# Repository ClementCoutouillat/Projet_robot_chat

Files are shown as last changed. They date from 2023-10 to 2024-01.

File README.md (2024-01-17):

# Projet_robot_chat

Projet fait par Quentin Henriet, Bastien Chinianga, Jiang Kaixuan, Jangbo Wang et Clément Coutouillat
Dans ce projet, nous devons réaliser un robot à propulsion différentielle à deux roues pour jouer au jeu du chat et de la souris. Lorsque le robot est le chat, il poursuit la souris, et lorsqu'il est la souris, il fuit le chat. Pour accomplir ce jeu, nous devons réaliser les parties suivantes :

- Le robot doit pouvoir changer de rôle entre chat et souris dans le jeu. Lorsque deux robots entrent en collision, leurs rôles changent - capteur de détection de collision.
- Le robot doit pouvoir se déplacer dans un environnement avec des limites, donc nous avons besoin d'un capteur de détection de bord - capteur de détection de bord.
- Le robot doit pouvoir détecter le chat ou la souris sur le terrain, donc nous avons besoin d'un capteur pour détecter les objets sur le terrain - capteur LIDAR.

## Ydlidar

Nous utilisons le LIDAR YDLIDAR X4 pour détecter l'autre robot sur le terrain.
D'après le manuel de données de YDLIDAR, nous savons que YDLIDAR utilise Uart pour la communication. Dans le manuel de développement, nous pouvons obtenir le format des données du LIDAR, comme illustré ci-dessous :
Lorsque nous envoyons la commande A5 60 au LIDAR, il renvoie une trame de données, dont le format est illustré ci-dessous :
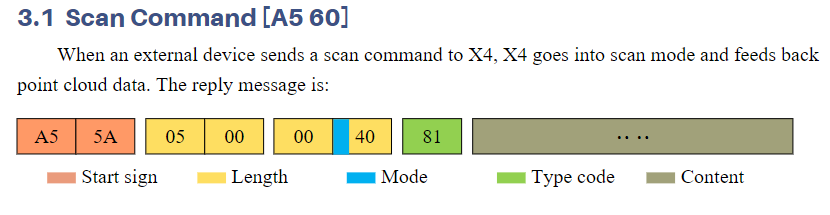
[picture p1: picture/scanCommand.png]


Ensuite, en suivant la méthode d'analyse du manuel de développement, nous obtenons les angles et les distances des obstacles de 0 à 360 degrés autour du robot, ce qui nous permet de localiser l'autre robot.
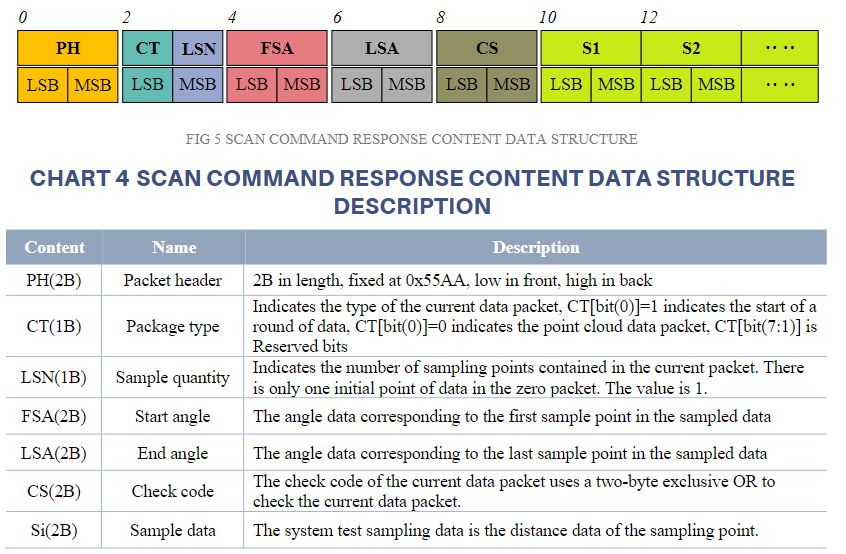
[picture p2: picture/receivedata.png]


## Stratégie

Dans le jeu, lorsque le robot est le chat, il doit poursuivre la souris, et lorsqu'il est la souris, il doit fuir le chat. Donc, selon le rôle du robot, nous avons besoin de stratégies différentes pour contrôler le mouvement du robot.

### Stratégie Chat

Lorsque le robot est le chat, il doit poursuivre la souris. Nous devons donc faire bouger le robot dans la direction de la souris. Tout d'abord, nous contrôlons la rotation du robot en calculant la différence d'angle entre le robot et la souris. Lorsque la souris se trouve entre 0 et 180 degrés, nous faisons tourner le robot à gauche. Lorsque l'autre robot se trouve entre 180 et 360 degrés, nous faisons tourner le robot

à droite. Une fois que le robot est orienté correctement, nous le faisons avancer jusqu'à ce qu'il entre en collision avec la souris. À ce moment-là, le rôle du robot change : le robot devient la souris et l'autre robot devient le chat. Nous pouvons alors utiliser la stratégie de la souris pour contrôler le mouvement du robot.

### Stratégie Souris

Lorsque le robot est la souris, il doit fuir le chat. Nous devons donc faire éloigner le robot du chat. Lorsqu'un chat se trouve à moins de 50 cm du robot et qu'il est situé entre 0 et 180 degrés, nous faisons tourner le robot à gauche de 90 degrés, puis le faisons avancer sur une certaine distance avant de le faire tourner à droite de 90 degrés. Cela permet au robot de s'éloigner du chat. Lorsque la distance entre le robot et le chat dépasse 50 cm, nous arrêtons le mouvement du robot. Lorsque le chat est situé entre 180 et 360 degrés, nous faisons tourner le robot à droite de 90 degrés, puis à gauche de 90 degrés, pour lui permettre de s'éloigner du chat.

## Moteur

Nous utilisons un robot à propulsion différentielle à deux roues, donc nous devons contrôler la vitesse des roues gauche et droite pour diriger le robot. Nous utilisons un moteur à courant continu à engrenages avec encodeur, dont la vitesse maximale est de 300 RPM.

### Avancer

Pour faire avancer le robot en ligne droite, nous contrôlons les vitesses des roues gauche et droite pour qu'elles soient identiques.

### Tourner

Le robot tourne en contrôlant la différence de vitesse entre les roues gauche et droite. Lorsque les vitesses des roues sont différentes, le robot tourne.

Nous utilisons une vitesse fixe pour contrôler la direction du robot. Lorsque le robot doit tourner à gauche, nous fixons la vitesse de la roue gauche à 0 et celle de la roue droite à la vitesse maximale. Lorsque le robot doit tourner à droite, nous fixons la vitesse de la roue droite à 0 et celle de la roue gauche à la vitesse maximale. Le temps nécessaire pour tourner est calculé avec la formule suivante :
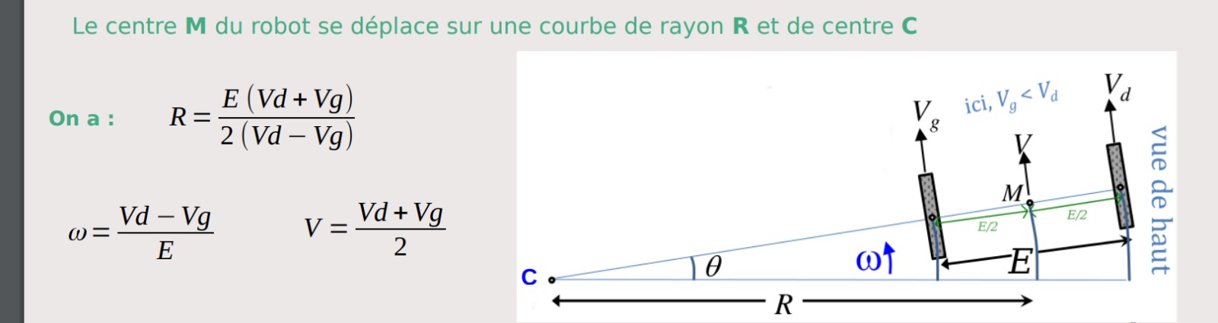
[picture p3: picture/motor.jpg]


<br />
leftWheelLinearVelocity = wheelDiameter * PI * leftWheelRPM / 60 ;
<br />
rightWheelLinearVelocity = wheelDiameter * PI * rightWheelRPM / 60 ;
<br />
angulaVelocity = (leftWheellinearVelocity - rightWheellinearVelocity) / WheelDistance ;
<br />
Timer = Angle(0-360) *PI / 180 / angulaVelocity ;

### Distance Control

La distance parcourue par le robot est contrôlée en gérant le temps de fonctionnement du robot. Lorsque le robot fonctionne pendant le temps que nous avons défini, il s'arrête. Cela permet de contrôler la distance parcourue par le robot. Le temps est calculé avec la formule suivante :
<br />
Timer = Distance / (WheelDiameter \* PI) / Vitesse ;

### Commande

Dans notre code pour manipuler le moteur, nous avons écrit deux fonctions. La première permet de contrôler directement la vitesse du moteur. Pour que le robot réponde plus rapidement aux commandes d'arrêt et d'accélération, nous avons également écrit une seconde fonction d'asservissement, qui utilise l'algorithme PID pour contrôler la rotation du moteur. Toutes les 100 ms, nous calculons la vitesse actuelle et fournissons un feedback sur la vitesse pour nous informer de la vitesse actuelle de rotation du moteur, ce qui nous permet de calculer plus précisément la position actuelle du robot et la distance parcourue. L'entrée du contrôleur PID est la vitesse cible du robot, et la sortie est la vitesse des roues gauche et droite du robot.

## Border

Pour les capteurs de bordure nous avons décidé d'utiliser les interruptions extérieures afin que la plus grande priorité possible et ne pas être interrompu durant le traitement de la détection de bordure. L'objectif était de pouvoir reculer et de tourner de 90 ou 180 degrés. Des tests ont été effectué sur une autre carte afin de vérifier le bon fonctionnement des fonctions. Malheureusement, les fonctions n'ont pas été implémenté sur la carte car les capteurs infrarouges étaient inutilisables et nous n'avions pas d'autres.

## Contact

Les capteurs de contact sont aussi branché sur les entrées GPIO du microprocesseur. Le contact permettant de gérer le mode chat ou souris, nous avons aussi décidé de les mettre en interruptions extérieur car ça simplifie le code avec juste une interruption qui préempte le code et une gestion de l'interruption. Il faut aussi mettre l'interruption des capteurs de bordure avec une plus haute priorité car c'est plus important de garder le robot sur le terrain que de savoir si on se fait toucher. Dans l'IOC il faut faire attention à comment sont régler les GPIO. Ils sont soit en pull-up ou pull-down. Afin de pour pouvoir résoudre le problème du fonctionnement des  capteurs de contact nous avons décidé de "simuler" le fait d'être touchés par un autre robot. C'est-à-dire quand nous sommes trop proches d'un autre robot nous considérons que nous avons été touché par celui-ci, car sinon le robot ne change jamais d'état.

## Accéléromètre

Au cours du projet nous avons utilisé deux cartes différentes. Sur la première, nous avions pensé à utiliser une centrale inertielle donc un accéléromètre et un gyroscope. Nous avons donc commencé l'écriture d'un driver( un .c et un .h) pour utiliser cet IMU. Malheureusement sur la nouvelle carte il n'y avait plus la possibilité d'utiliser un IMU, et vu l'inutilité de cette partie nous avons décidé de ne pas la mettre sur le github mais de quand même  mentionner le fait qu'un début de driver a été fait.

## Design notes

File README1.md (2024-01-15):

# Projet_robot_chat
Projet fait par Quentin Henriet, Bastien Chinianga, Jiang Kaixuan, Jangbo Wang et Clément Coutouillat
在这个项目中，我们需要完成一个两轮差分驱动的机器人来完成猫和老鼠的游戏。当机器人是猫时，它会追逐老鼠，当机器人是老鼠时，它会逃离猫。为了完成这个游戏，我们需要完成以下几个部分：
- 机器人能够在猫和老鼠的游戏中切换身份，当两个机器人发生碰撞时，它们的身份会发生变化--碰撞检测传感器
- 机器人能够在一个有边界的环境中移动，所以我们需要一个边界检测的传感器--边缘检测传感器
- 机器人能够检测到场地中的猫或者老鼠，所以我们需要一个传感器来检测场地中的物体--激光雷达传感器

## Ydlidar
* 我们使用YDLIDAR X4激光雷达来检测场地中的另一个机器人。
* 从YDLIDAR的数据手册中，我们知道YDLIDAR使用Uart进行通信，在开发手册中我们可以得到激光雷达的数据格式，如下图所示： 

当我们发送 A5 60 命令到激光雷达时，激光雷达会返回一帧数据，数据的格式如下图所示：

然后我们根据开发手册中的解析方法，得到机器人0-360度中的障碍物的角度和距离，从而得到另一个机器人的位置。

## 策略
在游戏中，当机器人是猫时，它会追逐老鼠，当机器人是老鼠时，它会逃离猫。所以针对机器人的不同身份，我们需要不同的策略来控制机器人的运动。
### Chat 策略
当机器人是猫时，它需要追逐老鼠，所以我们需要让机器人朝着老鼠的方向运动，首先我们通过计算机器人和老鼠的角度差来控制机器人向转到角度。当老鼠在0-180度之间时，我们让机器人向左转，当另一个机器人在180-360度之间时，我们让机器人向右转。当机器人转到正确的角度后，我们让机器人向前运动，直到机器人和老鼠发生碰撞，这时机器人的身份会发生变化，机器人变成老鼠，另一个机器人变成猫，然后我们就可以使用老鼠的策略来控制机器人的运动。
### Souris 策略
当机器人是老鼠时，它需要逃离猫，所以我们需要让机器人远离猫，当在机器人的50cm范围内有猫时且猫在0-180度之间时，我们让机器人向左转90读移动一段距离，然后再向右转90度移动一段距离，这样机器人就可以远离猫。当机器人和猫的距离大于50cm时，我们让机器人停止运动，当猫在180-360度之间时，我们让机器人向右转90度移动一段距离，然后再向左转90度移动一段距离，这样机器人就可以远离猫。当机器人和猫的距离大于50cm时，我们让机器人停止运动，当猫在180-360度之间时，我们让机器人向右转90度移动一段距离，然后再向左转90度移动一段距离，这样机器人就可以远离猫。 
## Motor
* 我们使用的是两轮差分驱动的机器人，所以我们需要控制机器人的左右轮的速度来控制机器人的运动。我们使用的是带有encoder的DC Geared Motor,它的最大转速300RPM 
### 前进
控制机器人的左右轮的速度相同，机器人就会直线运动。
### 转向
机器人的转向是通过控制机器人的左右轮的速度差来实现的，当机器人的左右轮的速度不同时，机器人会转向。
* 我们使用固定的速度来控制机器人的转向，当机器人需要向左转时，我们让机器人的左轮的速度为0，右轮的速度为最大速度，当机器人需要向右转时，我们让机器人的左轮的速度为最大速度，右轮的速度为0。转向需要的时间由下面的公式计算得到：

### 距离
机器人的距离是通过控制机器人运行的时间来实现的，当机器人运行的时间达到我们设定的时间时，机器人就会停止运动。从而实现机器人的距离控制。时间由下面的公式计算得到：
Timer = Distance / (WheelDiameter * PI) / Speed；
### 驱动
我们在对电机操作的代码中写了两个函数。一个是直接操控m改变电机的速度。为了使机器人更快的响应停止加速指令，其次我们也写了第二个asservissement的函数，使用pid算法控制电机的转动，每100ms会计算次当前的速度并进行feedback的返回速度让我们知道当前电机转动的速度，方便我们能够更精确的计算机器人的当前位置和运动的距离。PID控制器的输入是机器人的目标速度，输出是机器人的左右轮的速度。

## Border

## Contact

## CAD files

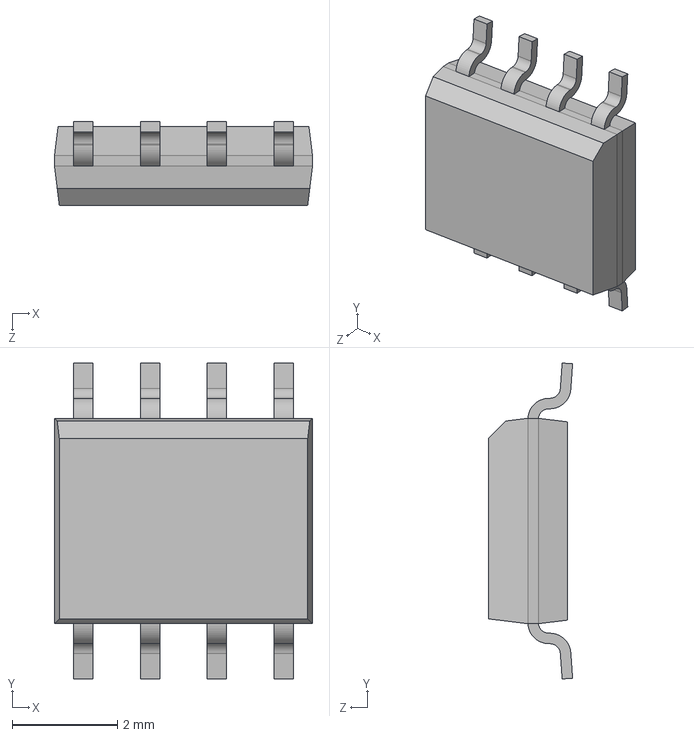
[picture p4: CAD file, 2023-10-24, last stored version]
Projet CTH-20231026T073019Z-001/Projet CTH/LIB_ACS711KLCTR-12AB-T/ACS711KLCTR-12AB-T/3D/ACS711KLCTR-12AB-T.stp
4.90 x 6.00 x 1.60 mm

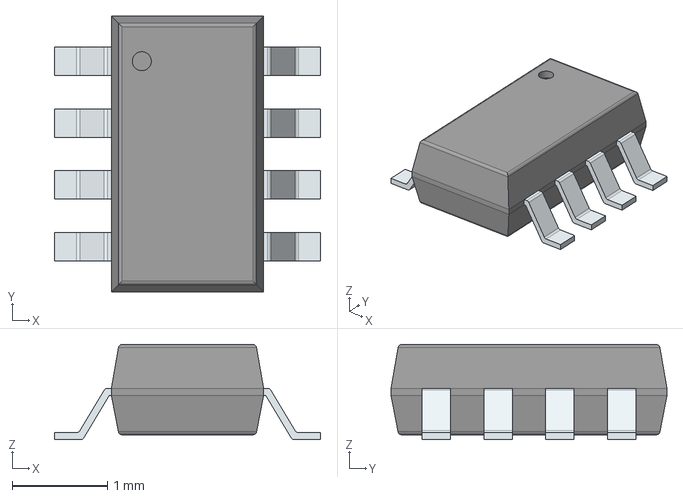
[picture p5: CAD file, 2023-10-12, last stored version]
Projet CTH-20231026T073019Z-001/Projet CTH/MP1475SGJ-P/3D/MP1475SGJ-P.stp
2.80 x 2.90 x 1.00 mm
PinsArrayLR

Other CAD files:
Projet CTH-20231026T073019Z-001/Projet CTH/MP1475SGJ-P/Allegro/sot65p280x100-8n.psm
Projet CTH-20231026T073019Z-001/Projet CTH/MP1475SGJ-P/DEHDL/mp1475sgj_p/chips/chips.prt
Projet CTH-20231026T073019Z-001/Projet CTH/projet moi/MP1475SGJ-P/Allegro/sot65p280x100-8n.psm
projet total 1 - Copie/MP1475SGJ-P/Allegro/sot65p280x100-8n.psm
projet total-20230929T114658Z-001/projet total/MP1475SGJ-P/Allegro/sot65p280x100-8n.psm
projet total-20230929T114658Z-001/projet total/MP1475SGJ-P/DEHDL/mp1475sgj_p/chips/chips.prt

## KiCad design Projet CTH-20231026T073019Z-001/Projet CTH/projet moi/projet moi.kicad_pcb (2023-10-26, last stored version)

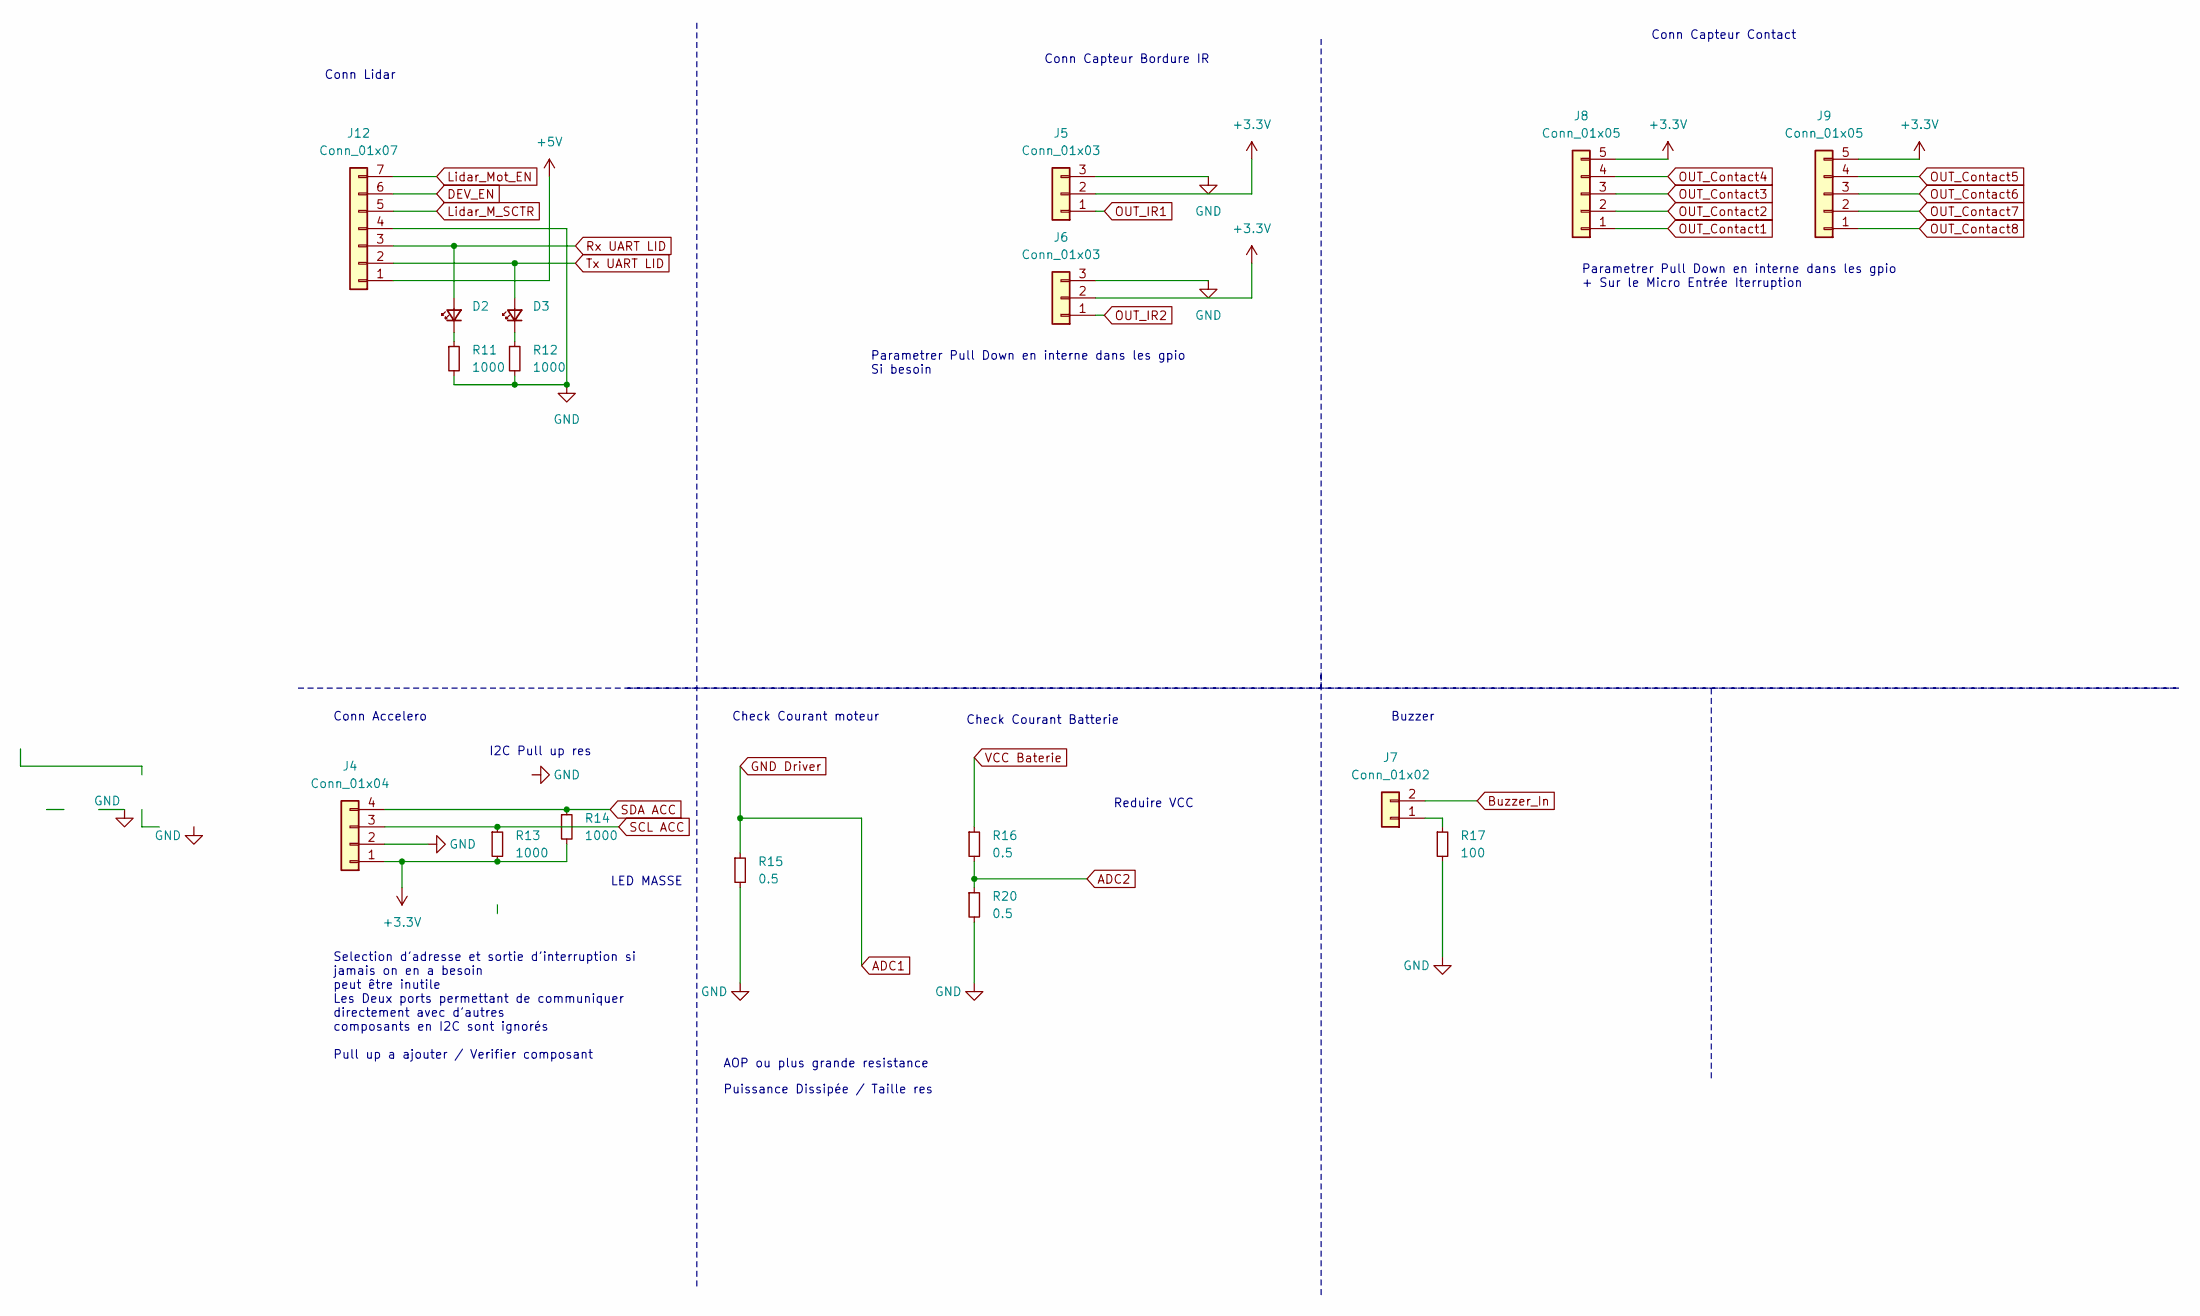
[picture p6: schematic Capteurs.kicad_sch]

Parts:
D2, D3: LED_Small; LED_0603_1608Metric_Pad1.05x0.95mm_HandSolder
J4: Conn_01x04; JST_EH_S4B-EH_1x04_P2.50mm_Horizontal
J5, J6: Conn_01x03; JST_XH_S3B-XH-A_1x03_P2.50mm_Horizontal
J7: Conn_01x02; JST_XH_S2B-XH-A_1x02_P2.50mm_Horizontal
J8, J9: Conn_01x05; JST_XH_S5B-XH-A_1x05_P2.50mm_Horizontal
J12: Conn_01x07; JST_XH_S7B-XH-A_1x07_P2.50mm_Horizontal
R11, R12, R13, R14: 1000; R_0603_1608Metric_Pad0.98x0.95mm_HandSolder
R15, R16, R20: 0.5; R_0603_1608Metric_Pad0.98x0.95mm_HandSolder
R17: 100; R_0603_1608Metric_Pad0.98x0.95mm_HandSolder

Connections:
7.2V: R16.1; also elsewhere on the board
+3.3V: J4.1, J5.2, J6.2, J8.5, J9.5, R13.2, R14.2; also elsewhere on the board
+5V: J12.1; also elsewhere on the board
ADC1: R15.1; also elsewhere on the board
ADC2: R16.2, R20.1; also elsewhere on the board
DEV_EN: J12.6; also elsewhere on the board
GND: J4.2, J5.3, J6.3, J12.4, R11.2, R12.2, R15.2, R17.2, R20.2; also elsewhere on the board
Lidar_M_SCTR: J12.5
Lidar_Mot_EN: J12.7
unnamed: D2.1 (K), R11.1
unnamed: D3.1 (K), R12.1
unnamed: J7.1, R17.1
OUT_Contact1: J8.1; also elsewhere on the board
OUT_Contact2: J8.2; also elsewhere on the board
OUT_Contact3: J8.3; also elsewhere on the board
OUT_Contact4: J8.4; also elsewhere on the board
OUT_Contact5: J9.4; also elsewhere on the board
OUT_Contact6: J9.3; also elsewhere on the board
OUT_Contact7: J9.2; also elsewhere on the board
OUT_Contact8: J9.1; also elsewhere on the board
OUT_IR1: J5.1; also elsewhere on the board
OUT_IR2: J6.1; also elsewhere on the board
Rx UART LID: D2.2 (A), J12.3; also elsewhere on the board
SCL ACC: J4.3, R13.1; also elsewhere on the board
SDA ACC: J4.4, R14.1; also elsewhere on the board
Tx UART LID: D3.2 (A), J12.2; also elsewhere on the board

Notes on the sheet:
Reduire VCC
Check Courant moteur
Buzzer
Parametrer Pull Down en interne dans les gpio + Sur le Micro Entrée Iterruption
Check Courant Batterie
AOP ou plus grande resistance
Puissance Dissipée / Taille res
Conn Lidar
Conn Accelero
Conn Capteur Contact
Parametrer Pull Down en interne dans les gpio Si besoin
I2C Pull up res
Selection d'adresse et sortie d'interruption si jamais on en a besoin peut être inutile Les Deux ports permettant de communiquer directement avec d'autres composants en I2C sont ignorés Pull up a ajouter / Verifier composant
LED MASSE
Conn Capteur Bordure IR

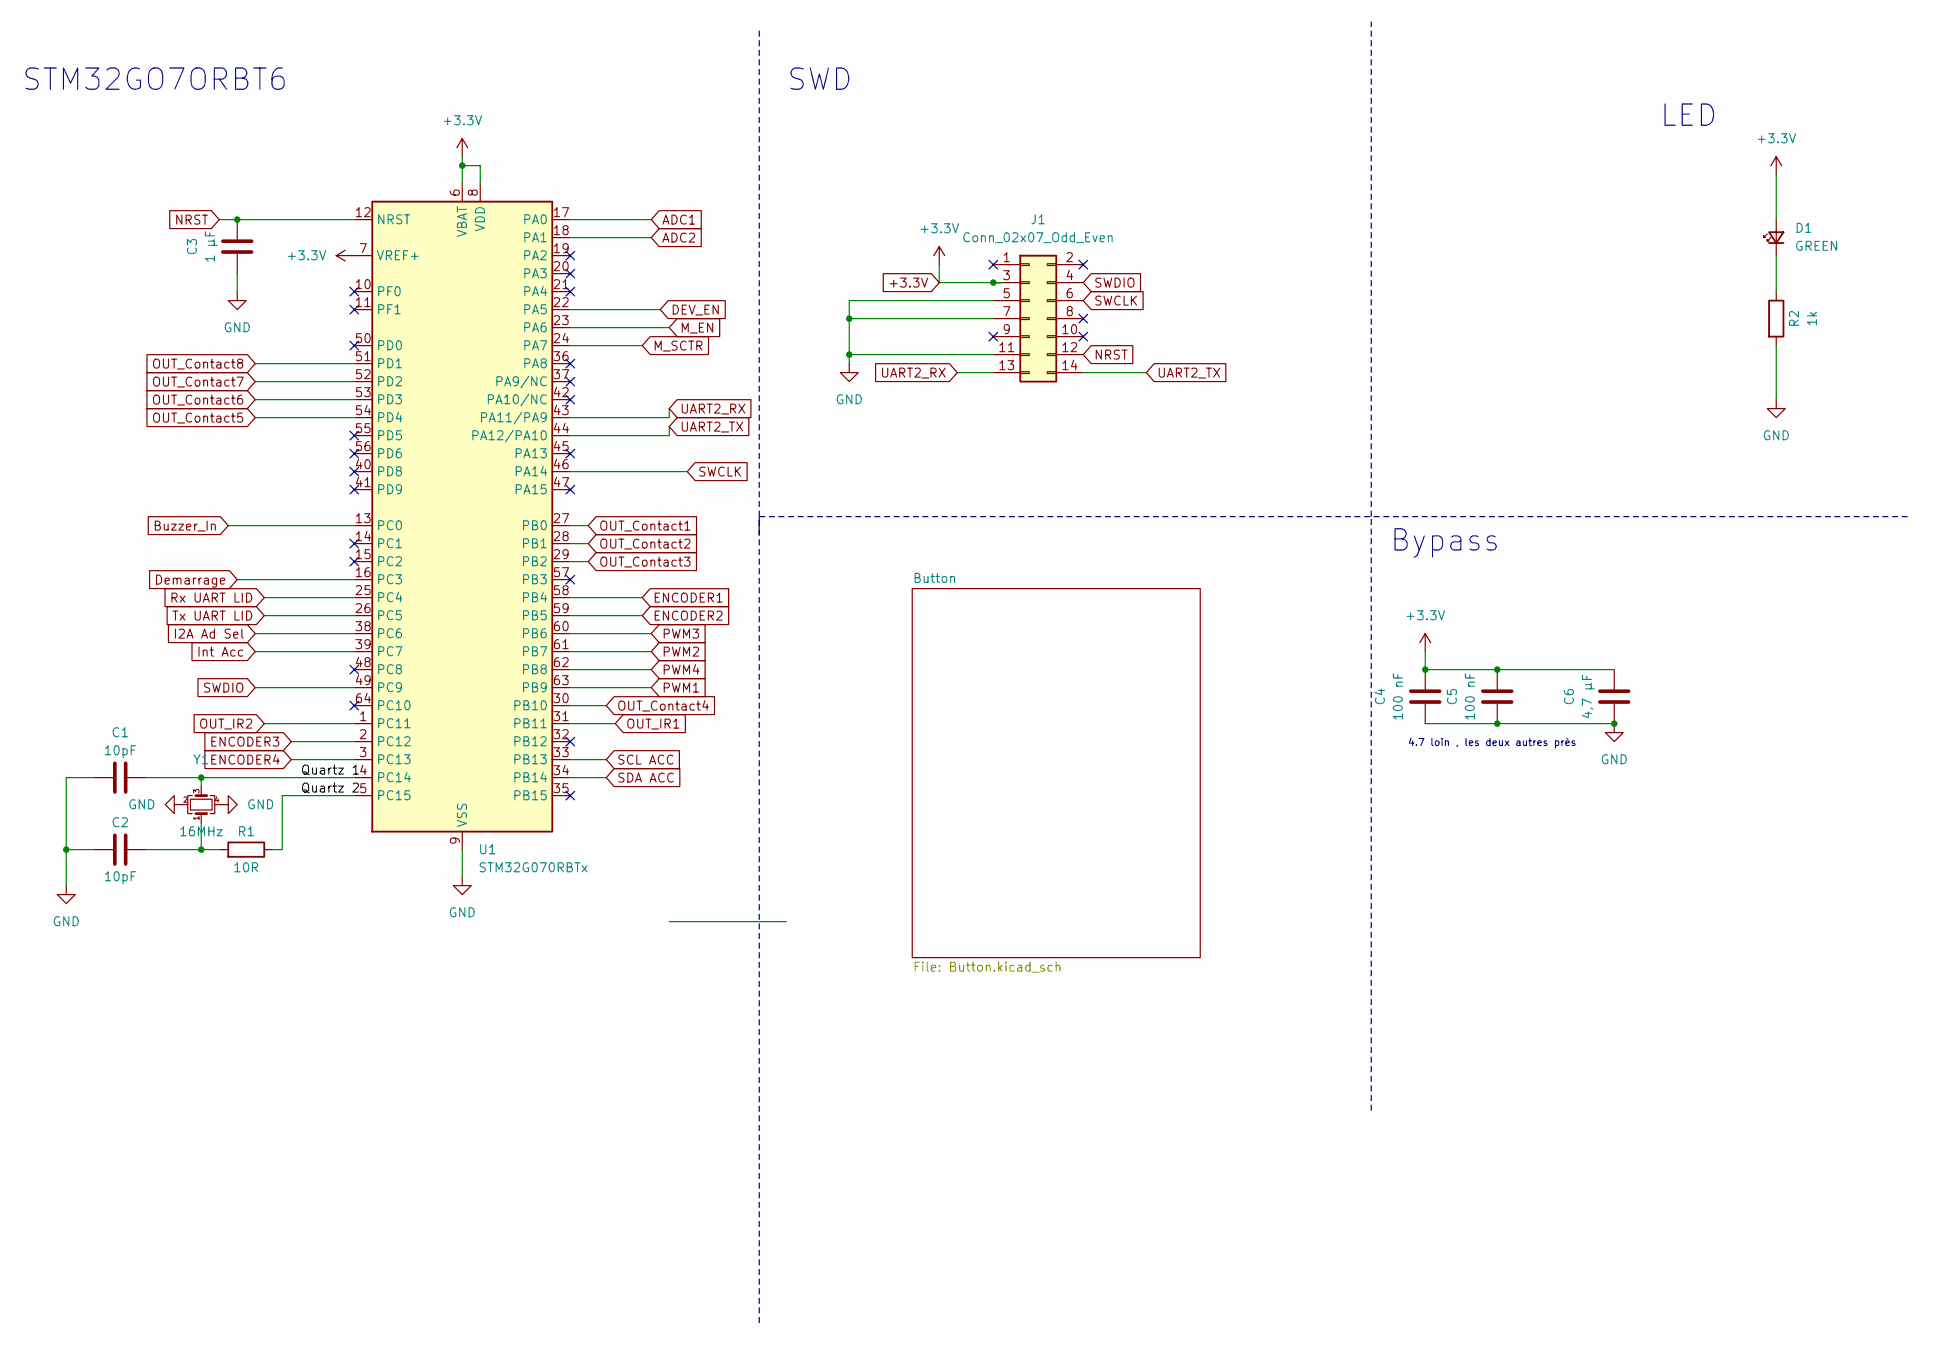
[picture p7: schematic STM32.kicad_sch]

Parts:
C1, C2: 10pF; C_0603_1608Metric_Pad1.08x0.95mm_HandSolder
C3: 1 µF; C_0603_1608Metric_Pad1.08x0.95mm_HandSolder
C4, C5: 100 nF; C_0603_1608Metric_Pad1.08x0.95mm_HandSolder
C6: 4,7 µF; C_0603_1608Metric_Pad1.08x0.95mm_HandSolder
D1: GREEN; LED_0603_1608Metric_Pad1.05x0.95mm_HandSolder
J1: Conn_02x07_Odd_Even; Molex_Nano-Fit_105314-xx14_2x07_P2.50mm_Horizontal
R1: 10R; R_0603_1608Metric_Pad0.98x0.95mm_HandSolder
R2: 1k; R_0603_1608Metric_Pad0.98x0.95mm_HandSolder
U1: STM32G070RBTx; LQFP-64_10x10mm_P0.5mm
Y1: 16MHz; Crystal_SMD_EuroQuartz_MT-4Pin_3.2x2.5mm

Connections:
+3.3V: C4.2, C5.2, C6.2, D1.2 (A), J1.3, U1.6 (VBAT), U1.7 (VREF+), U1.8 (VDD); also elsewhere on the board
/STM32/Quartz 1: C1.2, U1.4 (PC14), Y1.3
/STM32/Quartz 2: R1.1, U1.5 (PC15)
ADC1: U1.17 (PA0); also elsewhere on the board
ADC2: U1.18 (PA1); also elsewhere on the board
Buzzer_In: U1.13 (PC0)
DEV_EN: U1.22 (PA5); also elsewhere on the board
Demarrage: U1.16 (PC3); also elsewhere on the board
ENCODER1: U1.58 (PB4); also elsewhere on the board
ENCODER2: U1.59 (PB5); also elsewhere on the board
ENCODER3: U1.2 (PC12); also elsewhere on the board
ENCODER4: U1.3 (PC13); also elsewhere on the board
GND: C1.1, C2.1, C3.1, C4.1, C5.1, C6.1, J1.5, J1.7, J1.11, R2.2, U1.9 (VSS), Y1.2, Y1.4; also elsewhere on the board
I2A Ad Sel: U1.38 (PC6)
Int Acc: U1.39 (PC7)
M_EN: U1.23 (PA6)
M_SCTR: U1.24 (PA7)
NRST: C3.2, J1.12, U1.12 (NRST); also elsewhere on the board
unnamed: C2.2, R1.2, Y1.1
unnamed: D1.1 (K), R2.1
OUT_Contact1: U1.27 (PB0); also elsewhere on the board
OUT_Contact2: U1.28 (PB1); also elsewhere on the board
OUT_Contact3: U1.29 (PB2); also elsewhere on the board
OUT_Contact4: U1.30 (PB10); also elsewhere on the board
OUT_Contact5: U1.54 (PD4); also elsewhere on the board
OUT_Contact6: U1.53 (PD3); also elsewhere on the board
OUT_Contact7: U1.52 (PD2); also elsewhere on the board
OUT_Contact8: U1.51 (PD1); also elsewhere on the board
OUT_IR1: U1.31 (PB11); also elsewhere on the board
OUT_IR2: U1.1 (PC11); also elsewhere on the board
PWM1: U1.63 (PB9); also elsewhere on the board
PWM2: U1.61 (PB7); also elsewhere on the board
PWM3: U1.60 (PB6); also elsewhere on the board
PWM4: U1.62 (PB8); also elsewhere on the board
Rx UART LID: U1.25 (PC4); also elsewhere on the board
SCL ACC: U1.33 (PB13); also elsewhere on the board
SDA ACC: U1.34 (PB14); also elsewhere on the board
SWCLK: J1.6, U1.46 (PA14)
SWDIO: J1.4, U1.49 (PC9)
Tx UART LID: U1.26 (PC5); also elsewhere on the board
UART2_RX: J1.13, U1.43 (PA11/PA9)
UART2_TX: J1.14, U1.44 (PA12/PA10)

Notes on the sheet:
STM32GO7ORBT6
Bypass
LED
SWD
4.7 loin , les deux autres près

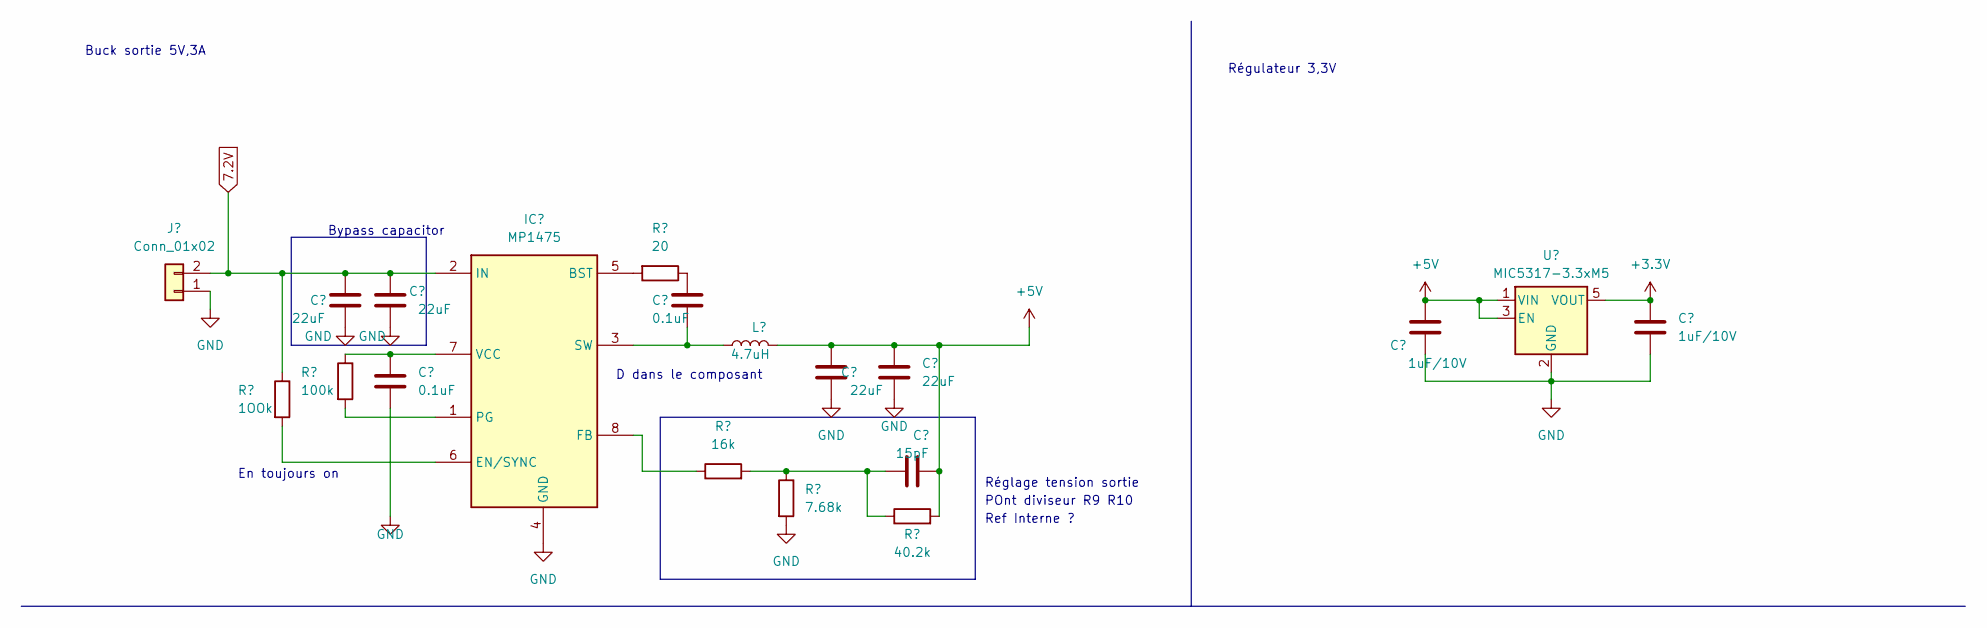
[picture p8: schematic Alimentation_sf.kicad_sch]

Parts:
C11, C12, C15, C16: 22uF; C_0603_1608Metric_Pad1.08x0.95mm_HandSolder
C13, C14: 0.1uF; C_0603_1608Metric_Pad1.08x0.95mm_HandSolder
C17: 15pF; C_0603_1608Metric_Pad1.08x0.95mm_HandSolder
C18, C19: 1uF/10V; C_0603_1608Metric_Pad1.08x0.95mm_HandSolder
IC1: MP1475; SOT65P280X100-8N; Mouser Part Number 946-MP1475SGJ-P
J2: Conn_01x02; JST_XH_S2B-XH-A_1x02_P2.50mm_Horizontal
L2: 4.7uH; L_0603_1608Metric_Pad1.05x0.95mm_HandSolder
R5: 1OOk; R_0603_1608Metric_Pad0.98x0.95mm_HandSolder
R6: 100k; R_0603_1608Metric_Pad0.98x0.95mm_HandSolder
R7: 20; R_0603_1608Metric_Pad0.98x0.95mm_HandSolder
R8: 16k; R_0603_1608Metric_Pad0.98x0.95mm_HandSolder
R9: 7.68k; R_0603_1608Metric_Pad0.98x0.95mm_HandSolder
R10: 40.2k; R_0603_1608Metric_Pad0.98x0.95mm_HandSolder
U2: MIC5317-3.3xM5; SOT-23-5

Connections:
7.2V: C11.1, C12.1, IC1.2 (IN), J2.2, R5.1; also elsewhere on the board
+3.3V: C19.1, U2.5 (VOUT); also elsewhere on the board
+5V: C15.1, C16.1, C17.2, C18.1, L2.2, R10.2, U2.1 (VIN), U2.3 (EN); also elsewhere on the board
GND: C11.2, C12.2, C13.2, C15.2, C16.2, C18.2, C19.2, IC1.4 (GND), J2.1, R9.2, U2.2 (GND); also elsewhere on the board
unnamed: C14.1, R7.1
unnamed: C17.1, R8.2, R9.1, R10.1
unnamed: IC1.5 (BST), R7.2
unnamed: IC1.6 (EN/SYNC), R5.2
unnamed: IC1.8 (FB), R8.1
unnamed: IC1.1 (PG), R6.2
unnamed: C14.2, IC1.3 (SW), L2.1
unnamed: C13.1, IC1.7 (VCC), R6.1

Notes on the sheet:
Bypass capacitor
POnt diviseur R9 R10
D dans le composant
En toujours on
Réglage tension sortie
Buck sortie 5V,3A
Régulateur 3,3V
Ref Interne ?

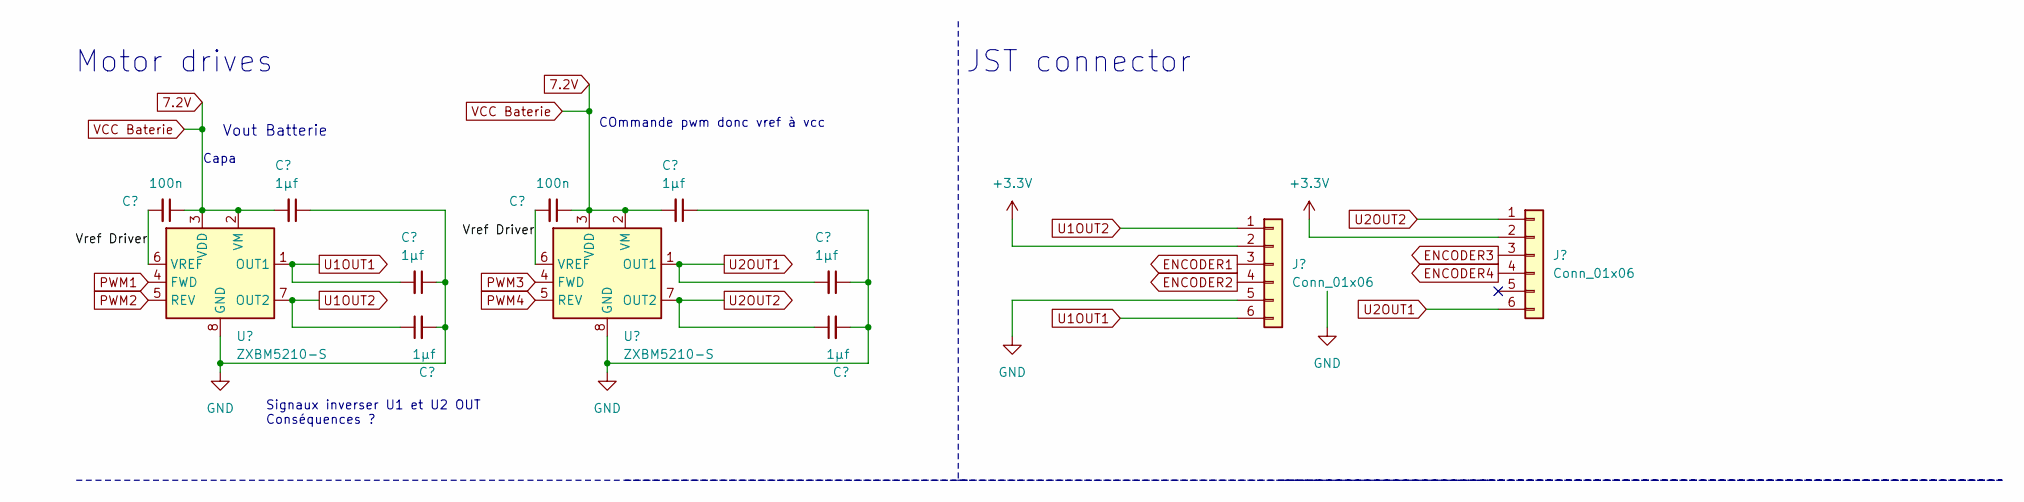
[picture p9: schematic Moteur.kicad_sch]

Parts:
C20, C21, C22, C23, C24, C25: 1µf; C_0603_1608Metric_Pad1.08x0.95mm_HandSolder
C27, C28: 100n; C_0603_1608Metric_Pad1.08x0.95mm_HandSolder
J10, J11: Conn_01x06; JST_XH_S6B-XH-A_1x06_P2.50mm_Horizontal
U3, U4: ZXBM5210-S; SOIC-8_3.9x4.9mm_P1.27mm

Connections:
7.2V: C20.2, C23.2, C27.1, C28.1, U3.2 (VM), U3.3 (VDD), U4.2 (VM), U4.3 (VDD); also elsewhere on the board
+3.3V: J10.2, J11.2; also elsewhere on the board
/Moteur/Vref Driver: C27.2, C28.2, U3.6 (VREF), U4.6 (VREF)
ENCODER1: J10.3; also elsewhere on the board
ENCODER2: J10.4; also elsewhere on the board
ENCODER3: J11.3; also elsewhere on the board
ENCODER4: J11.4; also elsewhere on the board
GND: C20.1, C21.1, C22.2, C23.1, C24.1, C25.2, J10.5, U3.8 (GND), U4.8 (GND); also elsewhere on the board
PWM1: U3.4 (FWD); also elsewhere on the board
PWM2: U3.5 (REV); also elsewhere on the board
PWM3: U4.4 (FWD); also elsewhere on the board
PWM4: U4.5 (REV); also elsewhere on the board
U1OUT1: C21.2, J10.6, U3.1 (OUT1)
U1OUT2: C22.1, J10.1, U3.7 (OUT2)
U2OUT1: C24.2, J11.6, U4.1 (OUT1)
U2OUT2: C25.1, J11.1, U4.7 (OUT2)

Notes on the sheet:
JST connector
Capa
Vout Batterie
Signaux inverser U1 et U2 OUT Conséquences ?
COmmande pwm donc vref à vcc
Motor drives

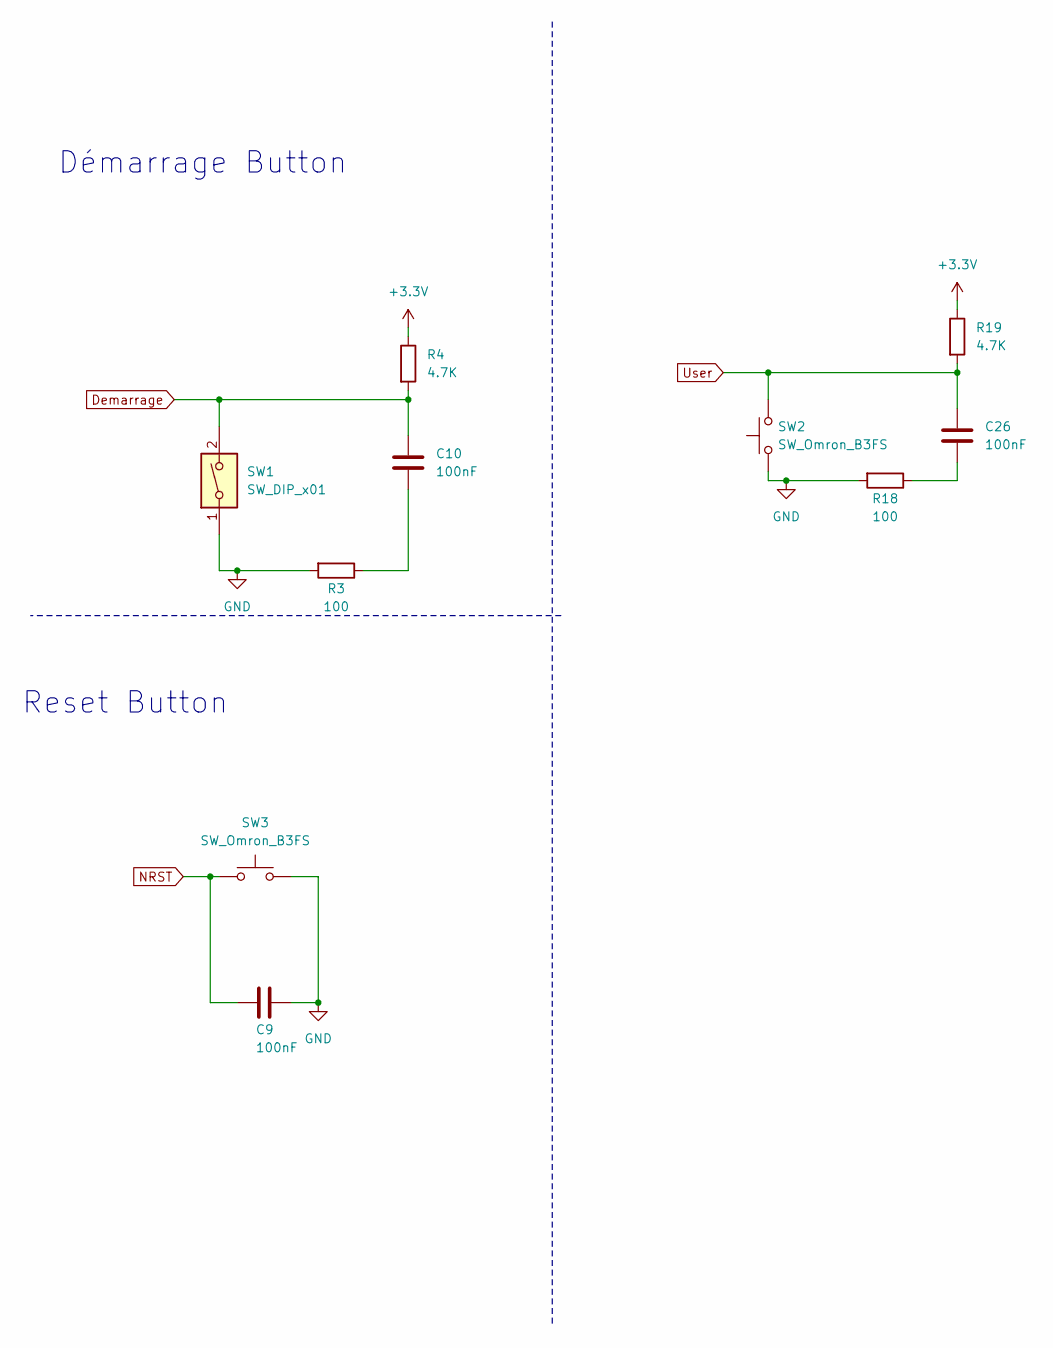
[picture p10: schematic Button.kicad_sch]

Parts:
C9, C10, C26: 100nF; C_0603_1608Metric_Pad1.08x0.95mm_HandSolder
R3, R18: 100; R_0603_1608Metric_Pad0.98x0.95mm_HandSolder
R4, R19: 4.7K; R_0603_1608Metric_Pad0.98x0.95mm_HandSolder
SW1: SW_DIP_x01; SW_SPST_B3U-1000P
SW2, SW3: SW_Omron_B3FS; SW_SPST_B3U-1000P

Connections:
+3.3V: R4.1, R19.1; also elsewhere on the board
Demarrage: C10.1, R4.2, SW1.2; also elsewhere on the board
GND: C9.1, R3.2, R18.2, SW1.1, SW2.1, SW3.2; also elsewhere on the board
NRST: C9.2, SW3.1; also elsewhere on the board
unnamed: C10.2, R3.1
unnamed: C26.2, R18.1
User: C26.1, R19.2, SW2.2

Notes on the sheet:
Démarrage Button
Reset Button

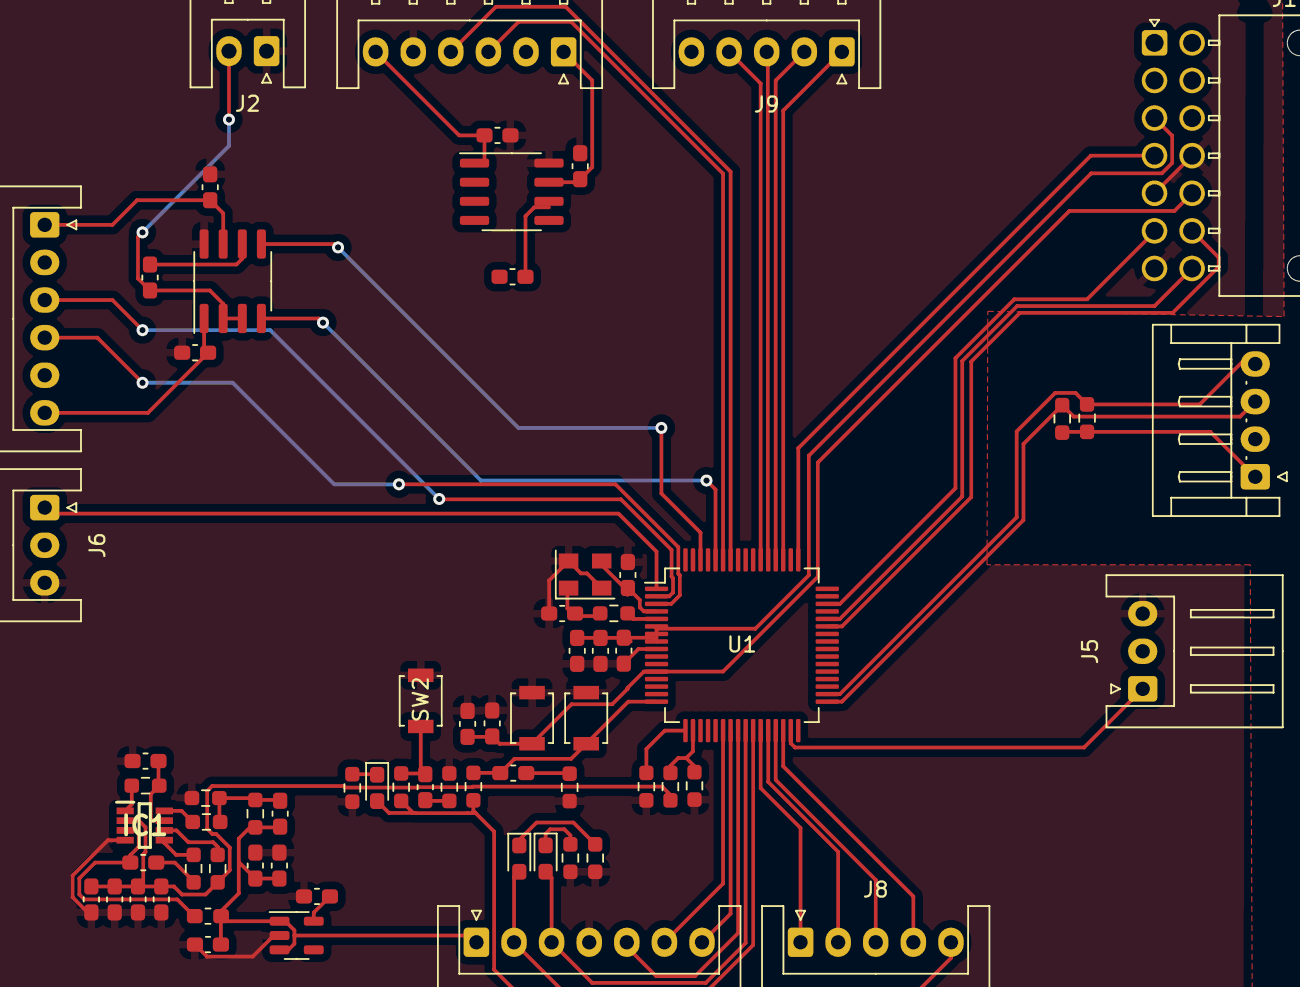
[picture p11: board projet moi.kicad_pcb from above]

Board: 4 copper layers, 68 parts (0 on the bottom side), 57 nets.

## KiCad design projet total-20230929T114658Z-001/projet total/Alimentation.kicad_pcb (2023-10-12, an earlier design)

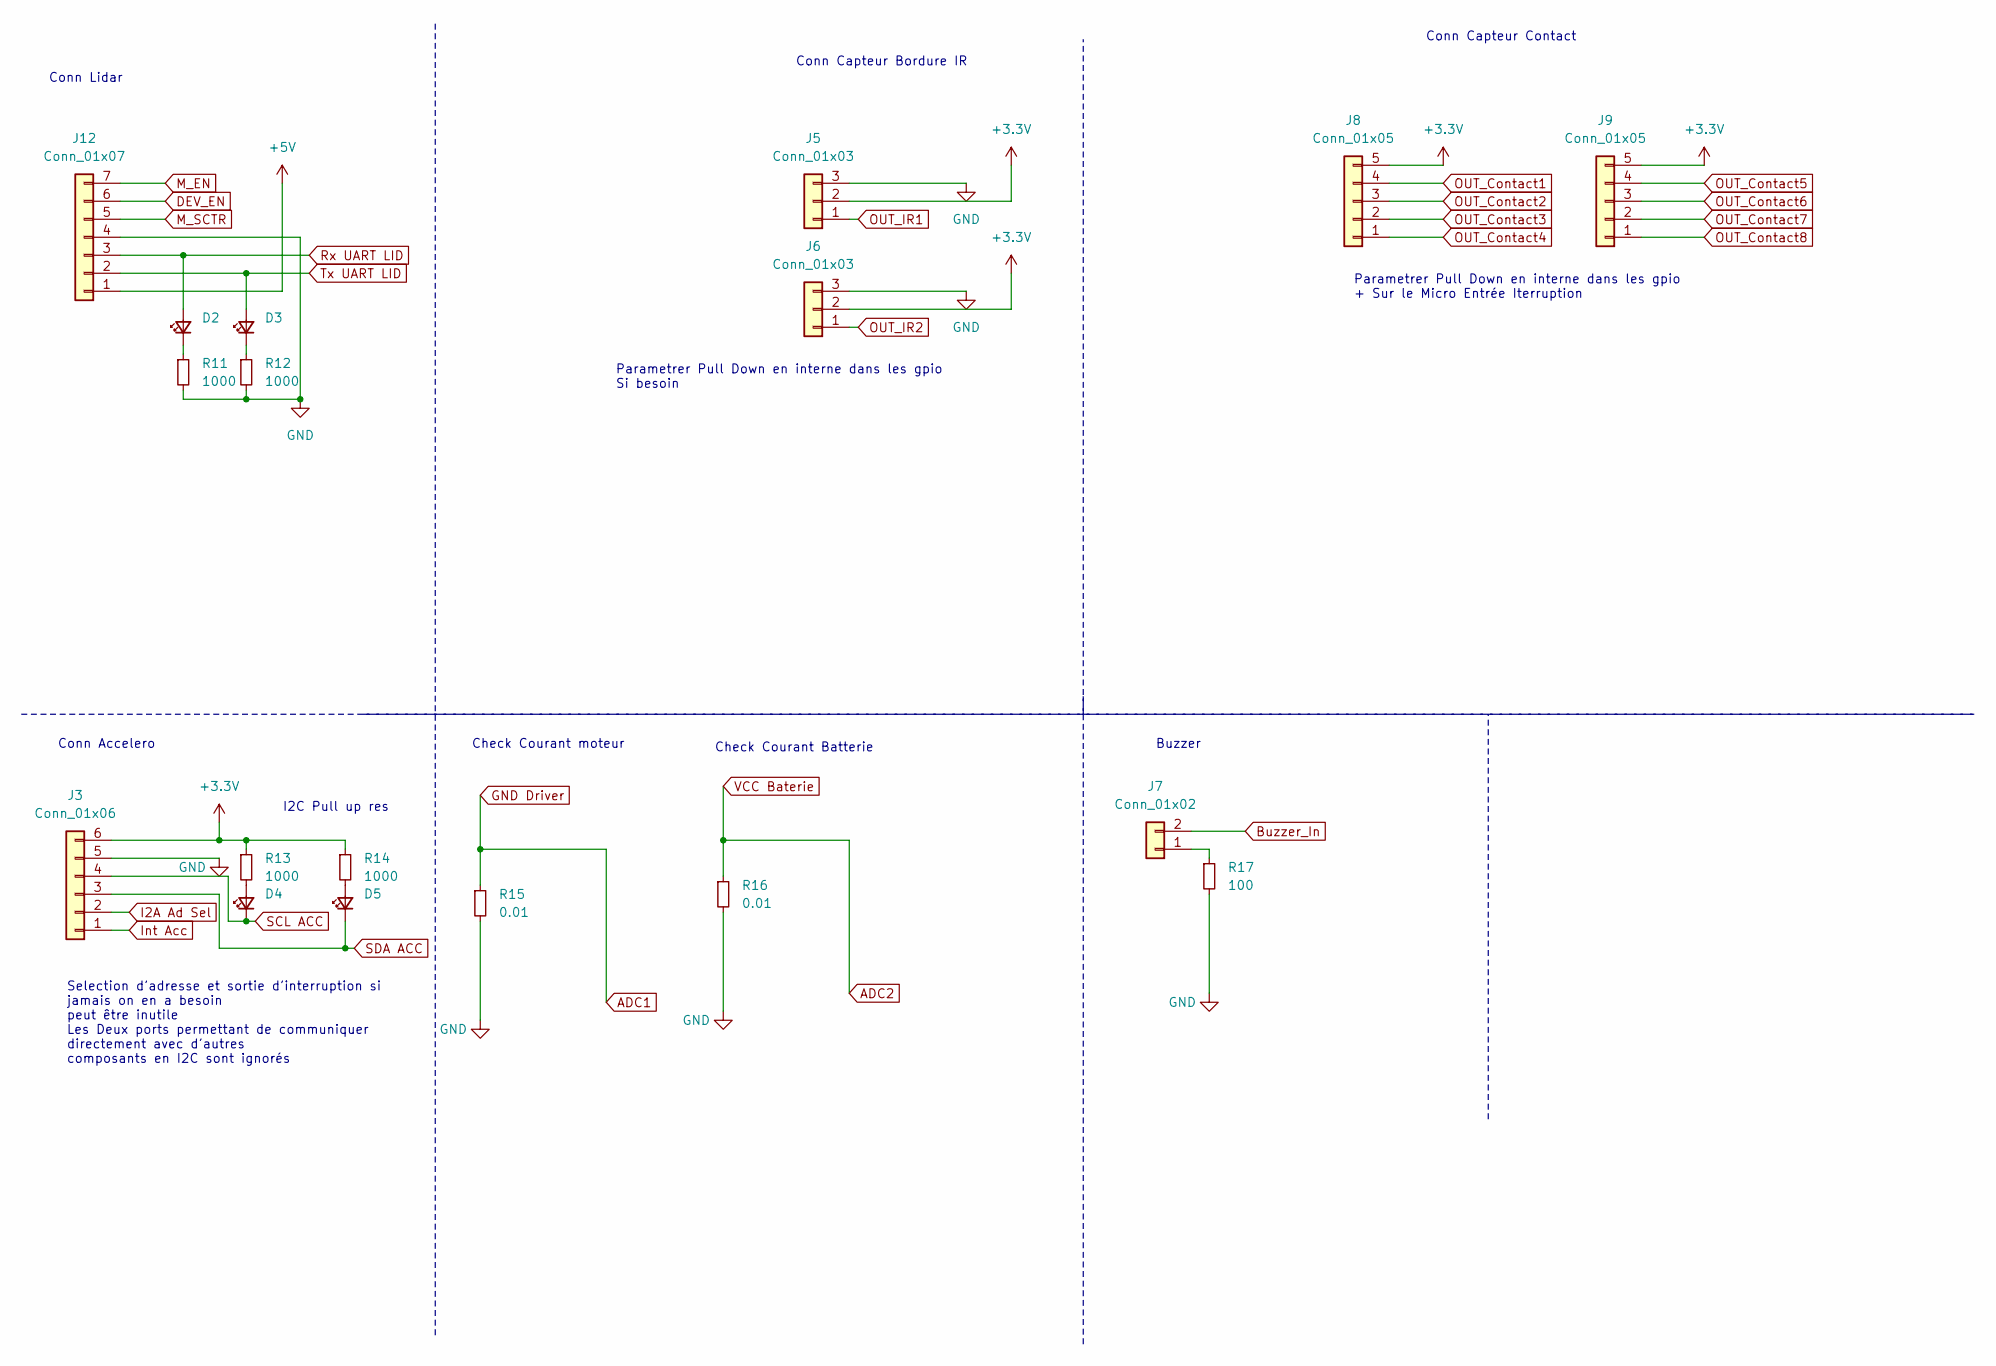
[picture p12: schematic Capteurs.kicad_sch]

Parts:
D2, D3, D4, D5: LED_Small; LED_0603_1608Metric_Pad1.05x0.95mm_HandSolder
J3: Conn_01x06; PinSocket_1x06_P2.54mm_Vertical
J5, J6: Conn_01x03; PinSocket_1x03_P2.54mm_Vertical
J7: Conn_01x02; PinSocket_1x02_P2.54mm_Vertical
J8, J9: Conn_01x05; PinSocket_1x05_P2.54mm_Vertical
J12: Conn_01x07; PinSocket_1x06_P2.54mm_Vertical
R11, R12, R13, R14: 1000; R_0603_1608Metric_Pad0.98x0.95mm_HandSolder
R15, R16: 0.01; R_0603_1608Metric_Pad0.98x0.95mm_HandSolder
R17: 100; R_0603_1608Metric_Pad0.98x0.95mm_HandSolder

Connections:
ADC1: R15.1; also elsewhere on the board
ADC2: R16.1; also elsewhere on the board
Buzzer_In: J7.2; also elsewhere on the board
GND: J3.5, J5.3, J6.3, J12.4, R11.2, R12.2, R15.2, R16.2, R17.2; also elsewhere on the board
I2A Ad Sel: J3.2; also elsewhere on the board
Int Acc: J3.1; also elsewhere on the board
unnamed: D2.1 (K), R11.1
unnamed: D3.1 (K), R12.1
unnamed: D4.2 (A), R13.2
unnamed: D5.2 (A), R14.2
unnamed: J7.1, R17.1
OUT_Contact1: J8.4; also elsewhere on the board
OUT_Contact2: J8.3; also elsewhere on the board
OUT_Contact3: J8.2; also elsewhere on the board
OUT_Contact4: J8.1; also elsewhere on the board
OUT_Contact5: J9.4; also elsewhere on the board
OUT_Contact6: J9.3; also elsewhere on the board
OUT_Contact7: J9.2; also elsewhere on the board
OUT_Contact8: J9.1; also elsewhere on the board
OUT_IR1: J5.1; also elsewhere on the board
OUT_IR2: J6.1; also elsewhere on the board
Rx UART LID: D2.2 (A), J12.3; also elsewhere on the board
SCL ACC: D4.1 (K), J3.4; also elsewhere on the board
SDA ACC: D5.1 (K), J3.3; also elsewhere on the board
Tx UART LID: D3.2 (A), J12.2; also elsewhere on the board

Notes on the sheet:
Check Courant moteur
Buzzer
Parametrer Pull Down en interne dans les gpio + Sur le Micro Entrée Iterruption
Check Courant Batterie
Conn Lidar
Conn Accelero
Conn Capteur Contact
Parametrer Pull Down en interne dans les gpio Si besoin
I2C Pull up res
Selection d'adresse et sortie d'interruption si jamais on en a besoin peut être inutile Les Deux ports permettant de communiquer directement avec d'autres composants en I2C sont ignorés
Conn Capteur Bordure IR

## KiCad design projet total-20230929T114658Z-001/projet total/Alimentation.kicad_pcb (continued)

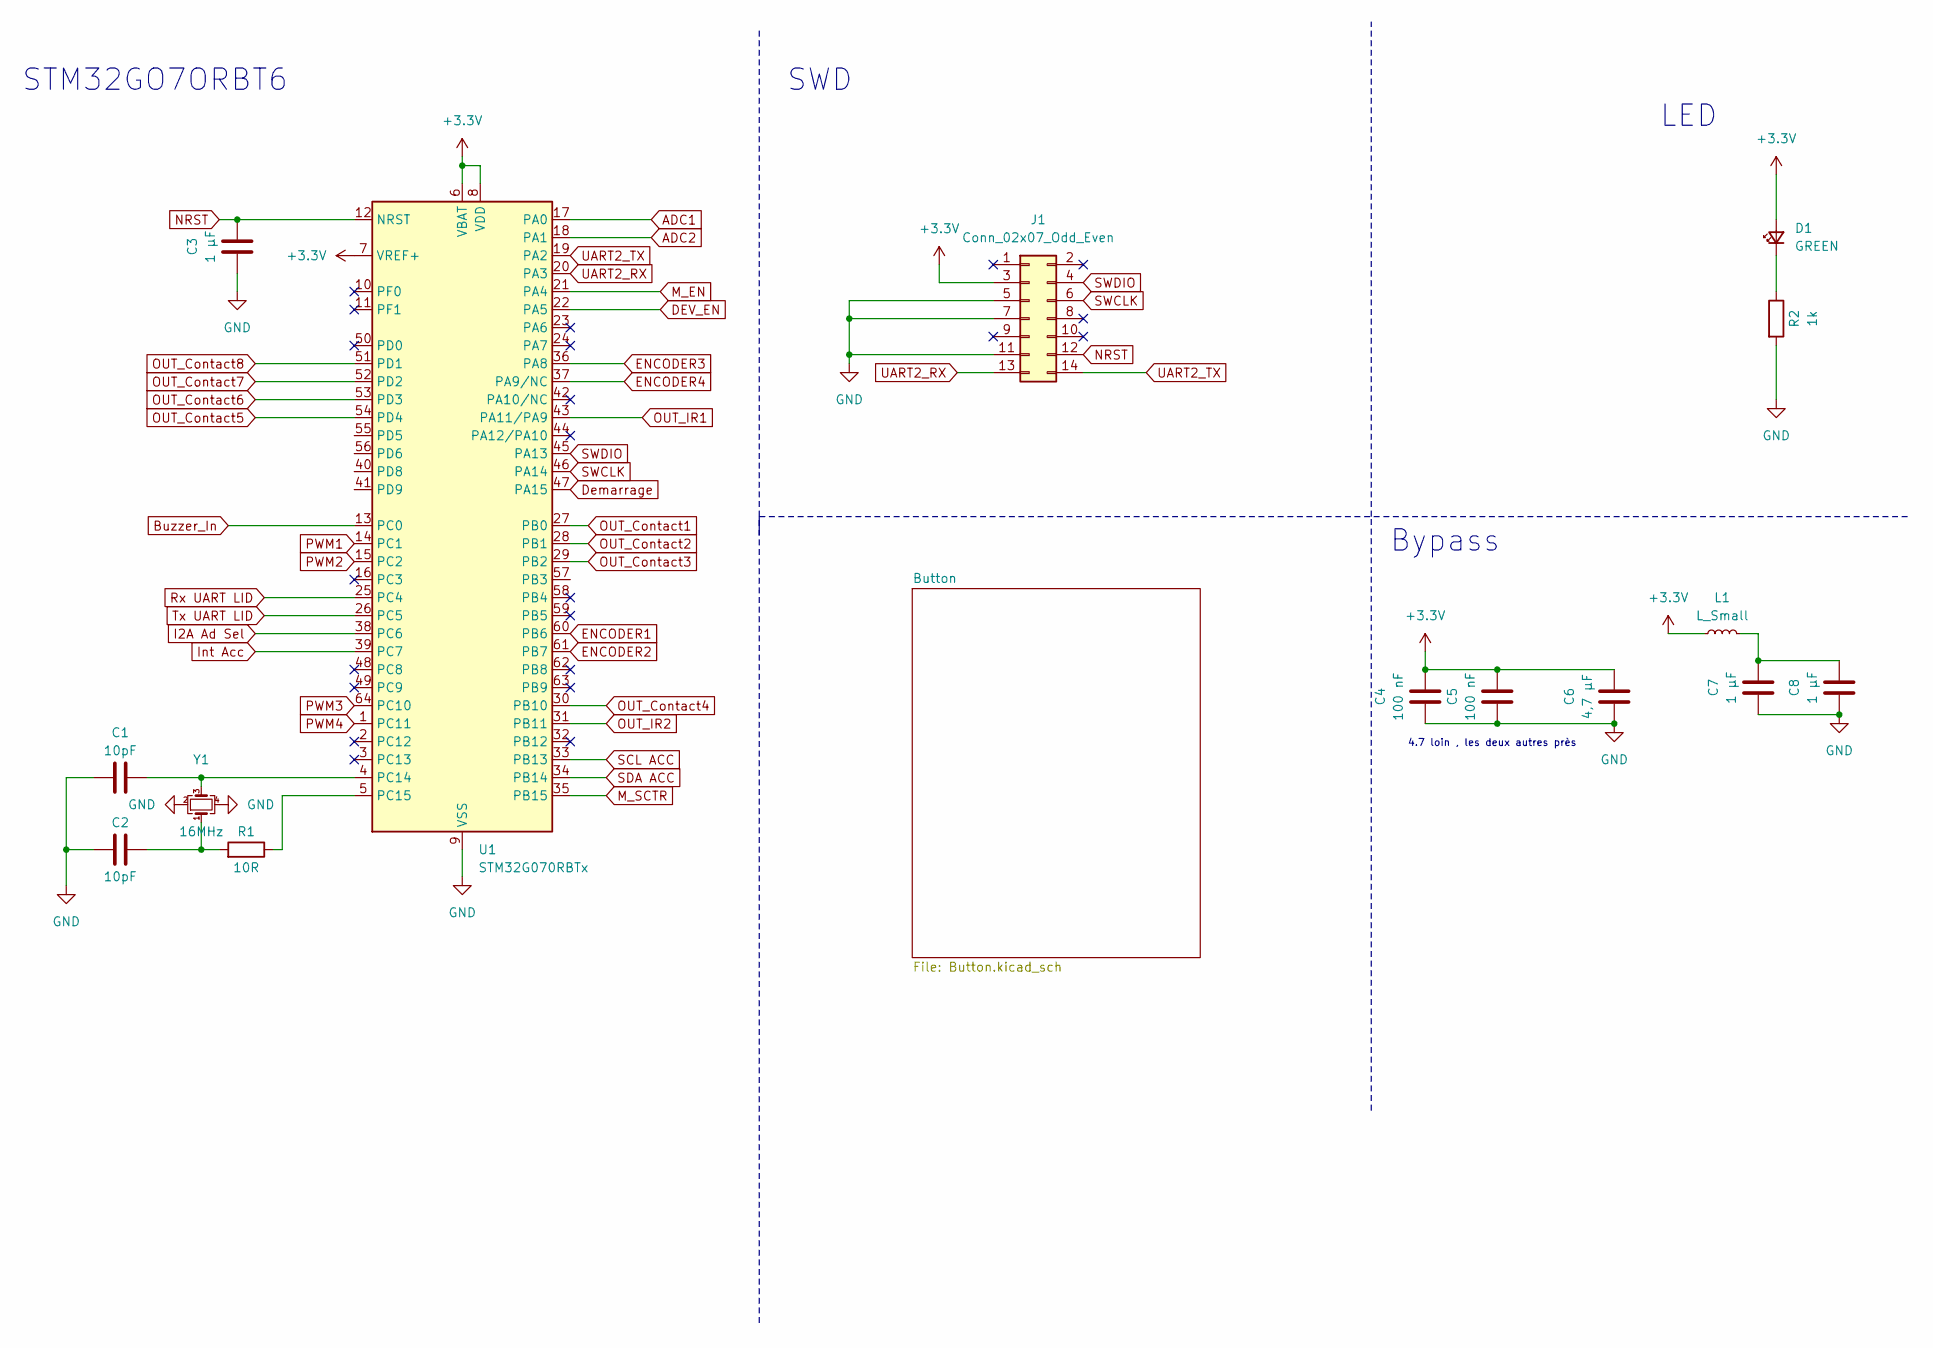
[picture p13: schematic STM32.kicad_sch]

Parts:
C1, C2: 10pF; C_0603_1608Metric_Pad1.08x0.95mm_HandSolder
C3, C7, C8: 1 µF; C_0603_1608Metric_Pad1.08x0.95mm_HandSolder
C4, C5: 100 nF; C_0603_1608Metric_Pad1.08x0.95mm_HandSolder
C6: 4,7 µF; C_0603_1608Metric_Pad1.08x0.95mm_HandSolder
D1: GREEN; LED_0603_1608Metric_Pad1.05x0.95mm_HandSolder
J1: Conn_02x07_Odd_Even; PinHeader_2x07_P1.27mm_Vertical_SMD
L1: L_Small; L_0603_1608Metric_Pad1.05x0.95mm_HandSolder
R1: 10R; R_0603_1608Metric_Pad0.98x0.95mm_HandSolder
R2: 1k; R_0603_1608Metric_Pad0.98x0.95mm_HandSolder
U1: STM32G070RBTx; LQFP-64_10x10mm_P0.5mm
Y1: 16MHz; Crystal_SMD_EuroQuartz_MT-4Pin_3.2x2.5mm

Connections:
ADC1: U1.17 (PA0); also elsewhere on the board
ADC2: U1.18 (PA1); also elsewhere on the board
Buzzer_In: U1.13 (PC0); also elsewhere on the board
DEV_EN: U1.22 (PA5); also elsewhere on the board
Demarrage: U1.47 (PA15); also elsewhere on the board
ENCODER1: U1.60 (PB6); also elsewhere on the board
ENCODER2: U1.61 (PB7); also elsewhere on the board
ENCODER3: U1.36 (PA8); also elsewhere on the board
ENCODER4: U1.37 (PA9/NC); also elsewhere on the board
GND: C1.1, C2.1, C3.1, C4.1, C5.1, C6.1, C7.1, C8.1, J1.5, J1.7, J1.11, R2.2, U1.9 (VSS), Y1.2, Y1.4; also elsewhere on the board
I2A Ad Sel: U1.38 (PC6); also elsewhere on the board
Int Acc: U1.39 (PC7); also elsewhere on the board
M_EN: U1.21 (PA4); also elsewhere on the board
M_SCTR: U1.35 (PB15); also elsewhere on the board
NRST: C3.2, J1.12, U1.12 (NRST); also elsewhere on the board
unnamed: C2.2, R1.2, Y1.1
unnamed: C7.2, C8.2, L1.2
unnamed: D1.1 (K), R2.1
unnamed: C1.2, U1.4 (PC14), Y1.3
unnamed: R1.1, U1.5 (PC15)
OUT_Contact1: U1.27 (PB0); also elsewhere on the board
OUT_Contact2: U1.28 (PB1); also elsewhere on the board
OUT_Contact3: U1.29 (PB2); also elsewhere on the board
OUT_Contact4: U1.30 (PB10); also elsewhere on the board
OUT_Contact5: U1.54 (PD4); also elsewhere on the board
OUT_Contact6: U1.53 (PD3); also elsewhere on the board
OUT_Contact7: U1.52 (PD2); also elsewhere on the board
OUT_Contact8: U1.51 (PD1); also elsewhere on the board
OUT_IR1: U1.43 (PA11/PA9); also elsewhere on the board
OUT_IR2: U1.44 (PA12/PA10); also elsewhere on the board
PWM1: U1.14 (PC1); also elsewhere on the board
PWM2: U1.15 (PC2); also elsewhere on the board
PWM3: U1.64 (PC10); also elsewhere on the board
PWM4: U1.1 (PC11); also elsewhere on the board
Rx UART LID: U1.25 (PC4); also elsewhere on the board
SCL ACC: U1.33 (PB13); also elsewhere on the board
SDA ACC: U1.34 (PB14); also elsewhere on the board
SWCLK: J1.6, U1.46 (PA14)
SWDIO: J1.4, U1.45 (PA13)
Tx UART LID: U1.26 (PC5); also elsewhere on the board
UART2_RX: J1.13, U1.20 (PA3)
UART2_TX: J1.14, U1.19 (PA2)

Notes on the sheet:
STM32GO7ORBT6
Bypass
LED
SWD
4.7 loin , les deux autres près

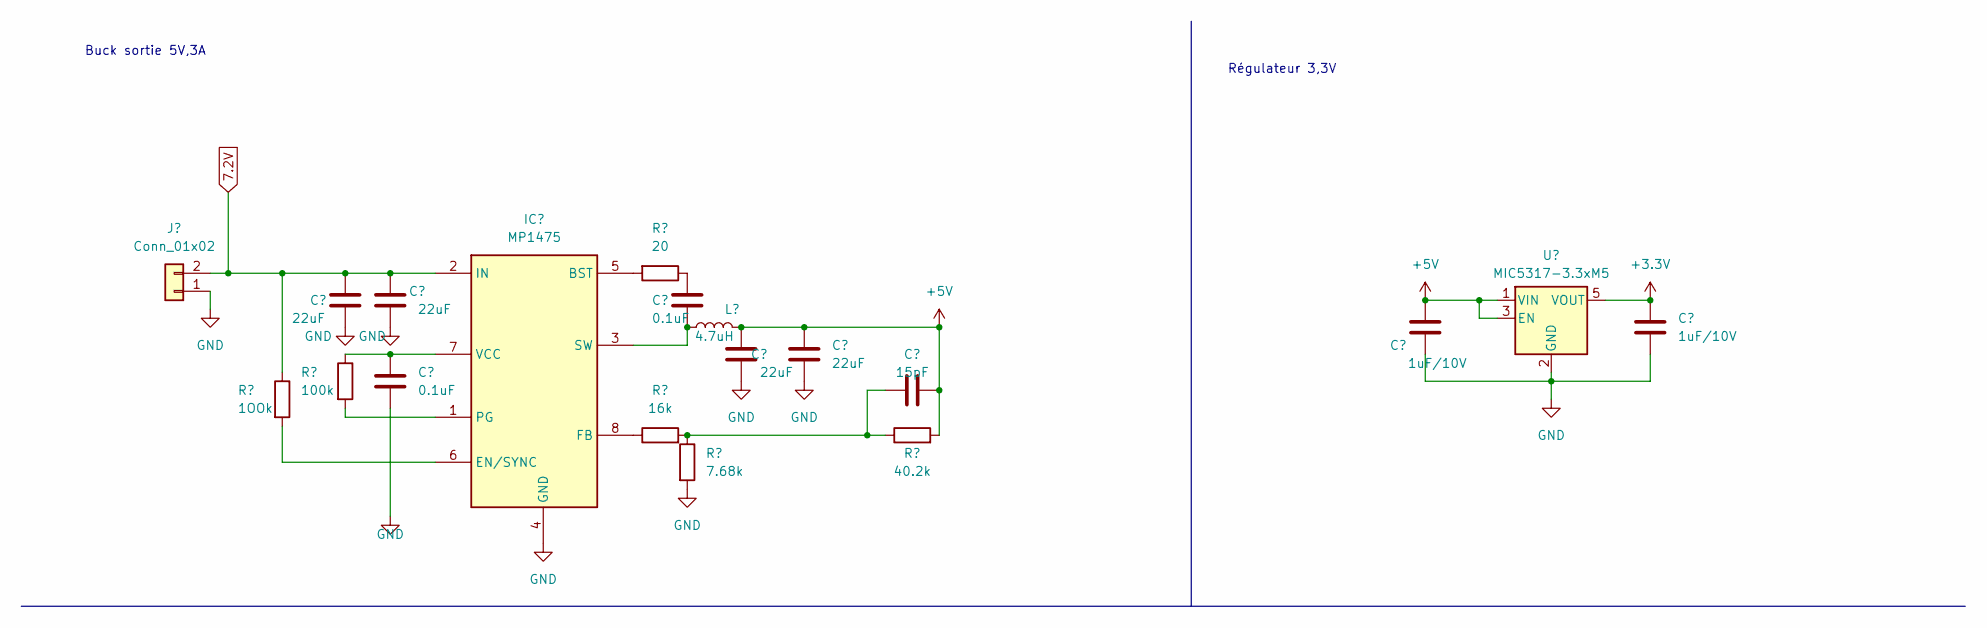
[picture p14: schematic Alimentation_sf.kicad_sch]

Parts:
C11, C12, C15, C16: 22uF; C_0603_1608Metric_Pad1.08x0.95mm_HandSolder
C13, C14: 0.1uF; C_0603_1608Metric_Pad1.08x0.95mm_HandSolder
C17: 15pF; C_0603_1608Metric_Pad1.08x0.95mm_HandSolder
C18, C19: 1uF/10V; C_0603_1608Metric_Pad1.08x0.95mm_HandSolder
IC1: MP1475; SOT65P280X100-8N; Mouser Part Number 946-MP1475SGJ-P
J2: Conn_01x02; PinSocket_1x02_P2.54mm_Vertical
L2: 4.7uH; L_0603_1608Metric_Pad1.05x0.95mm_HandSolder
R5: 1OOk; R_0603_1608Metric_Pad0.98x0.95mm_HandSolder
R6: 100k; R_0603_1608Metric_Pad0.98x0.95mm_HandSolder
R7: 20; R_0603_1608Metric_Pad0.98x0.95mm_HandSolder
R8: 16k; R_0603_1608Metric_Pad0.98x0.95mm_HandSolder
R9: 7.68k; R_0603_1608Metric_Pad0.98x0.95mm_HandSolder
R10: 40.2k; R_0603_1608Metric_Pad0.98x0.95mm_HandSolder
U2: MIC5317-3.3xM5; SOT-23-5

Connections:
7.2V: C11.1, C12.1, IC1.2 (IN), J2.2, R5.1; also elsewhere on the board
+5V: C15.1, C16.1, C17.2, C18.1, L2.2, R10.2, U2.1 (VIN), U2.3 (EN); also elsewhere on the board
GND: C11.2, C12.2, C13.2, C15.2, C16.2, C18.2, C19.2, IC1.4 (GND), J2.1, R9.2, U2.2 (GND); also elsewhere on the board
unnamed: C14.1, R7.1
unnamed: C17.1, R8.2, R9.1, R10.1
unnamed: IC1.5 (BST), R7.2
unnamed: IC1.6 (EN/SYNC), R5.2
unnamed: IC1.8 (FB), R8.1
unnamed: IC1.1 (PG), R6.2
unnamed: C14.2, IC1.3 (SW), L2.1
unnamed: C13.1, IC1.7 (VCC), R6.1

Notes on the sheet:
Buck sortie 5V,3A
Régulateur 3,3V

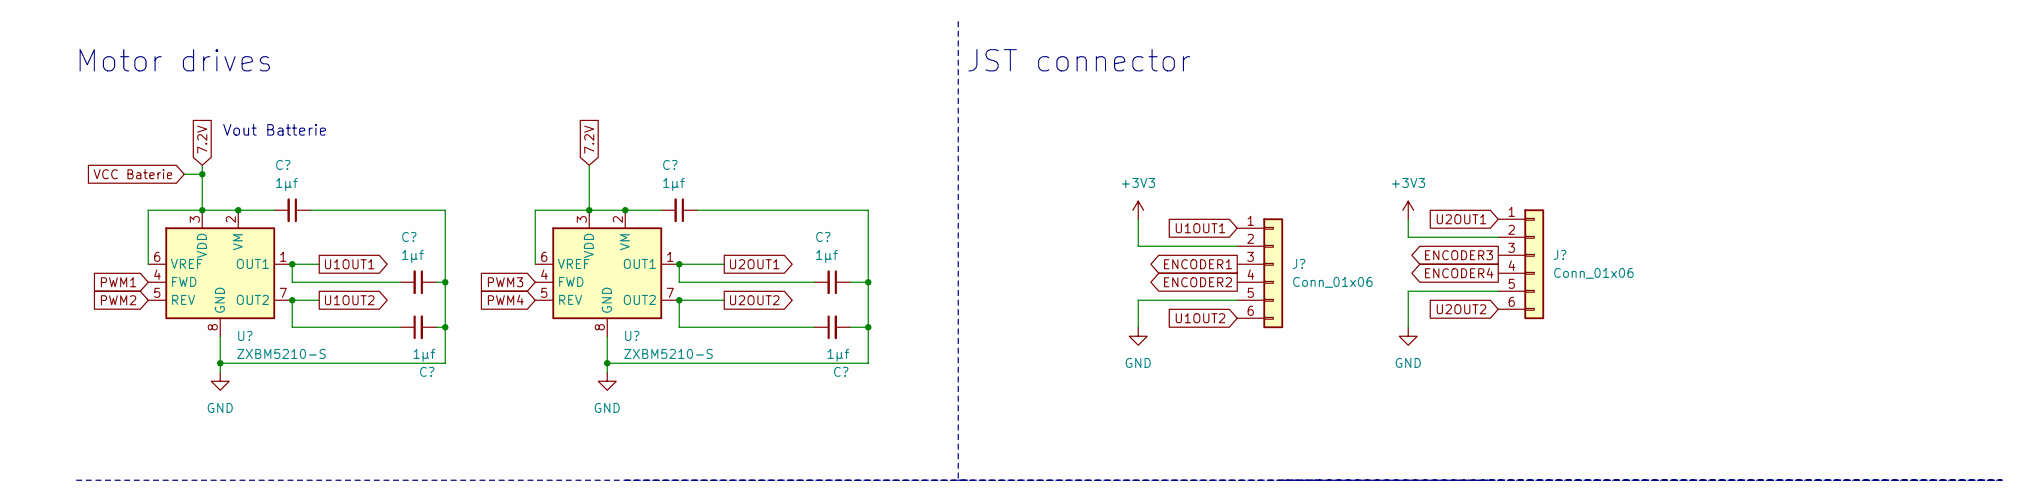
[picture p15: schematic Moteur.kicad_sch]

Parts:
C20, C21, C22, C23, C24, C25: 1µf; C_0603_1608Metric_Pad1.08x0.95mm_HandSolder
J10, J11: Conn_01x06; PinSocket_1x06_P2.54mm_Vertical
U3, U4: ZXBM5210-S; SOIC-8_3.9x4.9mm_P1.27mm

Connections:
7.2V: C20.2, C23.2, U3.2 (VM), U3.3 (VDD), U3.6 (VREF), U4.2 (VM), U4.3 (VDD), U4.6 (VREF); also elsewhere on the board
ENCODER1: J10.3; also elsewhere on the board
ENCODER2: J10.4; also elsewhere on the board
ENCODER3: J11.3; also elsewhere on the board
ENCODER4: J11.4; also elsewhere on the board
GND: C20.1, C21.1, C22.2, C23.1, C24.1, C25.2, J10.5, J11.5, U3.8 (GND), U4.8 (GND); also elsewhere on the board
PWM1: U3.4 (FWD); also elsewhere on the board
PWM2: U3.5 (REV); also elsewhere on the board
PWM3: U4.4 (FWD); also elsewhere on the board
PWM4: U4.5 (REV); also elsewhere on the board
U1OUT1: C21.2, J10.1, U3.1 (OUT1)
U1OUT2: C22.1, J10.6, U3.7 (OUT2)
U2OUT1: C24.2, J11.1, U4.1 (OUT1)
U2OUT2: C25.1, J11.6, U4.7 (OUT2)

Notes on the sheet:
JST connector
Vout Batterie
Motor drives

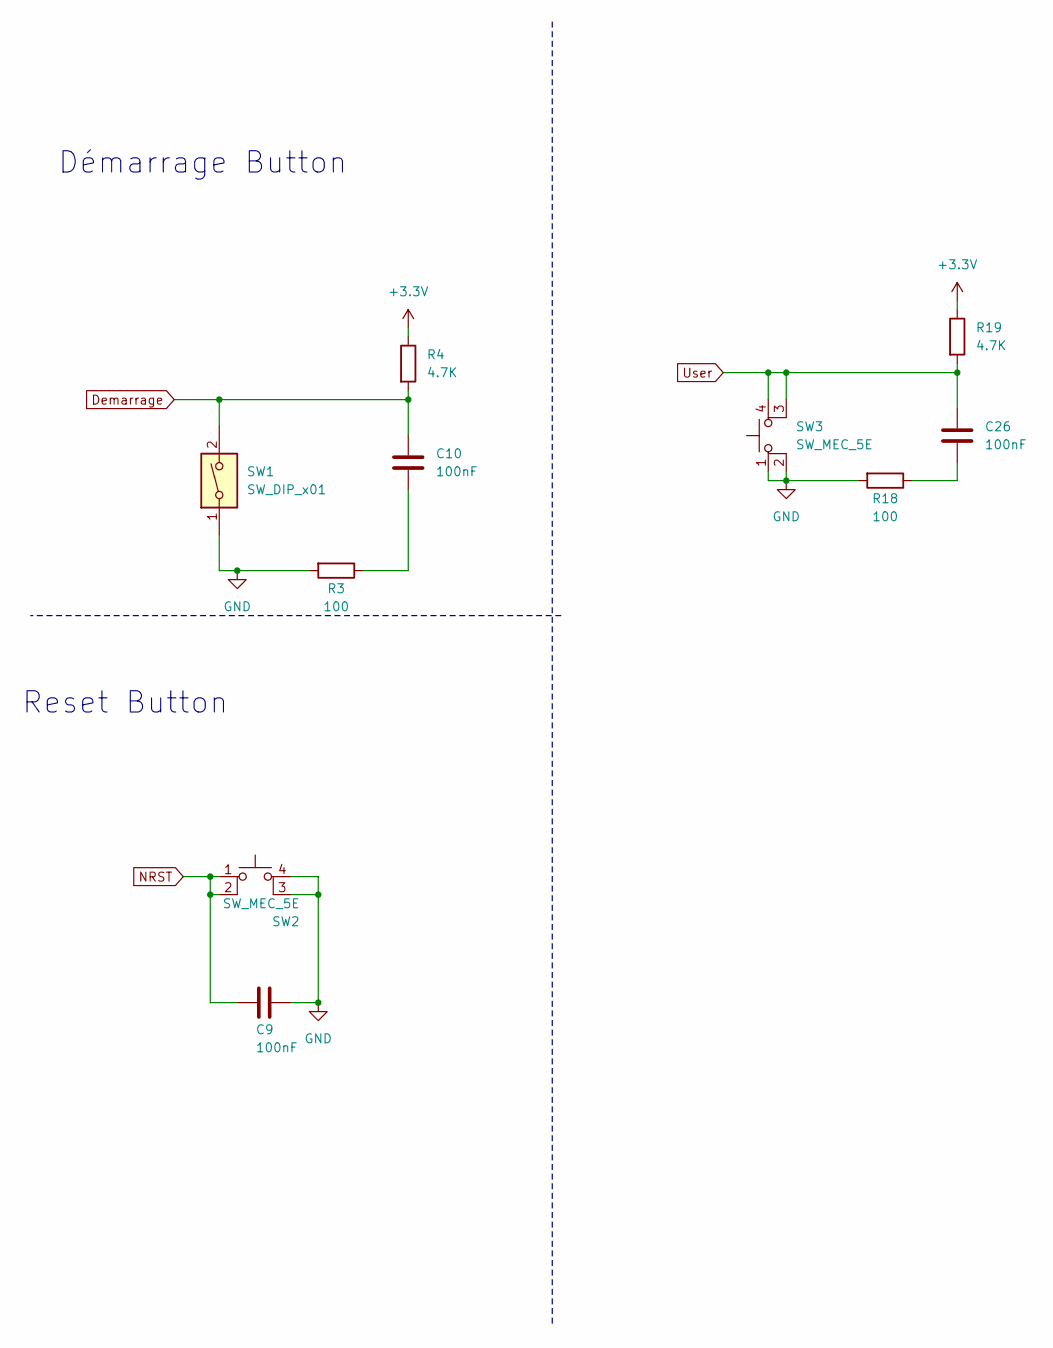
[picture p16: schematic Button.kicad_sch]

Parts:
C9, C10, C26: 100nF; C_0603_1608Metric_Pad1.08x0.95mm_HandSolder
R3, R18: 100; R_0603_1608Metric_Pad0.98x0.95mm_HandSolder
R4, R19: 4.7K; R_0603_1608Metric_Pad0.98x0.95mm_HandSolder
SW1: SW_DIP_x01; SW_SPST_B3U-1000P
SW2, SW3: SW_MEC_5E; SW_SPST_B3U-1000P

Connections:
Demarrage: C10.1, R4.2, SW1.2; also elsewhere on the board
GND: C9.1, R3.2, R18.2, SW1.1, SW2.3 (K), SW2.4 (A), SW3.1, SW3.2; also elsewhere on the board
NRST: C9.2, SW2.1, SW2.2; also elsewhere on the board
unnamed: C10.2, R3.1
unnamed: C26.2, R18.1
User: C26.1, R19.2, SW3.3 (K), SW3.4 (A)

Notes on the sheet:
Démarrage Button
Reset Button

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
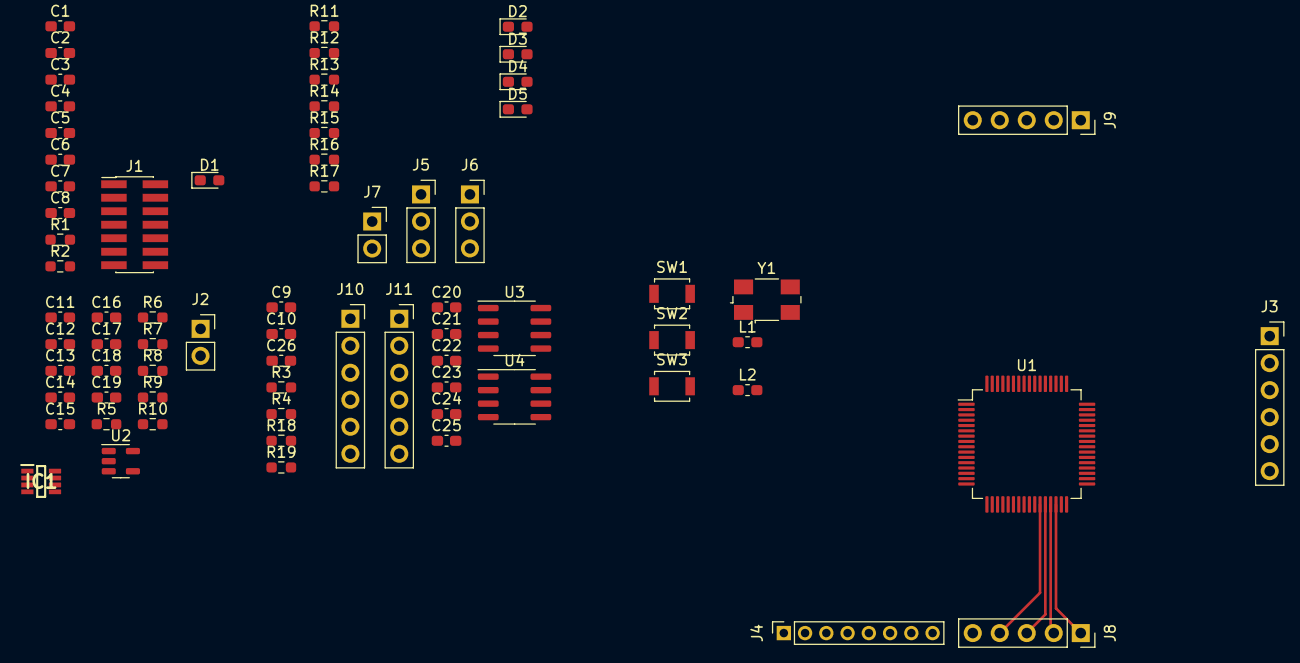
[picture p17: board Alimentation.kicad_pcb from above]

Board: 2 copper layers, 72 parts (0 on the bottom side), 66 nets.

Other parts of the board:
J4: Conn_01x08; PinSocket_1x08_P2.00mm_Vertical

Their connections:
+5V: J4.1; also elsewhere on the board
DEV_EN: J4.6; also elsewhere on the board
GND: J4.4; also elsewhere on the board
M_EN: J4.7; also elsewhere on the board
M_SCTR: J4.5; also elsewhere on the board
Rx UART LID: J4.3; also elsewhere on the board
Tx UART LID: J4.2; also elsewhere on the board

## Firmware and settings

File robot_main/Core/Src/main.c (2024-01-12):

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
/* Includes ------------------------------------------------------------------*/
#include "main.h"
#include "cmsis_os.h"
#include "dma.h"
#include "tim.h"
#include "usart.h"
#include "gpio.h"

/* USER CODE BEGIN Includes */
#include "led.h"
#include "shell_founction.h"
#include "ydlidar.h"
#include "board.h"
#include "bumper.h"
#include "dcMotor.h"
#include "system.h"
#include "motorInterface.h"
/* USER CODE END Includes */


void SystemClock_Config(void);
void MX_FREERTOS_Init(void);
/* USER CODE BEGIN 0 */
// Task handle
TaskHandle_t StartTask_Handler;
void start_task(void *pvParameters)
{
    taskENTER_CRITICAL(); // enter critical section
    // Create LED task
    createLedTask();
    // Create shell task
    // createShellTask();
    // create motor task
    // createDcMotorTask();
    // Create board task
    // createBoardTask();
    // Create bumper task
    // createBumperTask();
    // Create ydlidar task
    createYdlidarTask();
    // Create avoid task
    createSystemTask();
    // delete start task
    vTaskDelete(StartTask_Handler); // delete start task
    taskEXIT_CRITICAL();            // exit critical section
}

/* USER CODE END 0 */

/**
  * @brief  The application entry point.
  * @retval int
  */
int main(void)
{
  /* MCU Configuration--------------------------------------------------------*/

  /* Reset of all peripherals, Initializes the Flash interface and the Systick. */
  HAL_Init();

  /* Configure the system clock */
  SystemClock_Config();

  /* Initialize all configured peripherals */
  MX_GPIO_Init();
  MX_DMA_Init();
  MX_TIM17_Init();
  MX_TIM15_Init();
  MX_TIM16_Init();
  MX_TIM1_Init();
  MX_TIM3_Init();
  MX_USART2_UART_Init();
  MX_USART4_UART_Init();
  /* USER CODE BEGIN 2 */
    // encoder mode using PA8 for the input signal,and PA8 is also using for the syscfg register,so we need to disable the syscfg register[8]
    SYSCFG->CFGR1 |= (1 << 9);
    printf("\r\n\r\n>>>>>>>>>>>>>>Projet Robot Start<<<<<<<<<<<<<<\r\n");
    // system init
    systemInit();
    // HAL_Delay(5000);
    // while (1)
    // {
    //     moteur_controle_dPWM(190, 250);
    //     HAL_Delay(2000);
    //     motorStop();
    //     HAL_Delay(2000);
    // }

    xTaskCreate((TaskFunction_t)start_task, // task function
                (const char *)"start_task", // task name
                (uint16_t)256,              // stack size
                (void *)NULL,               // parameter
                (UBaseType_t)1,             // priority
                (TaskHandle_t *)&StartTask_Handler);
    vTaskStartScheduler();

  /* USER CODE END 2 */

  /* Call init function for freertos objects (in freertos.c) */
  MX_FREERTOS_Init();

  /* Start scheduler */
  osKernelStart();

  /* We should never get here as control is now taken by the scheduler */
  /* Infinite loop */
  /* USER CODE BEGIN WHILE */
    while (1)
    {
    /* USER CODE END WHILE */

    /* USER CODE BEGIN 3 */
    }
  /* USER CODE END 3 */
}

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
/**
  * @brief  Period elapsed callback in non blocking mode
  * @note   This function is called  when TIM6 interrupt took place, inside
  * HAL_TIM_IRQHandler(). It makes a direct call to HAL_IncTick() to increment
  * a global variable "uwTick" used as application time base.
  * @param  htim : TIM handle
  * @retval None
  */
void HAL_TIM_PeriodElapsedCallback(TIM_HandleTypeDef *htim)
{
  if (htim->Instance == TIM6) {
    HAL_IncTick();
  }
  /* USER CODE BEGIN Callback 1 */
    if (htim->Instance == TIM3) // encooder compter  motor 1
    {
        //   Determine the current counter counting direction
        if (__HAL_TIM_IS_TIM_COUNTING_DOWN(htim))
        //     underflow, count down
        {
            Encoder_Overflow_Count--;
        }
        else
        {
            //   overflow, count up
            Encoder_Overflow_Count++;
        }
    }
    else if (htim->Instance == TIM1) // encooder compter  motor 1
    {
        /* Determine the current counter counting direction */
        if (__HAL_TIM_IS_TIM_COUNTING_DOWN(htim))
        /* underflow, count down */
        {
            Encoder_Overflow_Count2--;
        }
        else
        {
            /* overflow, count up */
            Encoder_Overflow_Count2++;
        }
    }
  /* USER CODE END Callback 1 */
}

/**
  * @brief  This function is executed in case of error occurrence.
  * @retval None
  */
void Error_Handler(void)
{
  /* USER CODE BEGIN Error_Handler_Debug */
    /* User can add his own implementation to report the HAL error return state */
    __disable_irq();
    while (1)
    {
        HAL_GPIO_TogglePin(LED_ORANGE_GPIO_Port, LED_ORANGE_Pin);
        printf("error\r\n");
    }
  /* USER CODE END Error_Handler_Debug */
}

#ifdef  USE_FULL_ASSERT
/**
  * @brief  Reports the name of the source file and the source line number
  *         where the assert_param error has occurred.
  * @param  file: pointer to the source file name
  * @param  line: assert_param error line source number
  * @retval None
  */
void assert_failed(uint8_t *file, uint32_t line)
{
  /* USER CODE BEGIN 6 */
    /* User can add his own implementation to report the file name and line number,
       ex: printf("Wrong parameters value: file %s on line %d\r\n", file, line) */
  /* USER CODE END 6 */
}
#endif /* USE_FULL_ASSERT */

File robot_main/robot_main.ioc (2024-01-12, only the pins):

Mcu.UserName=STM32G070RBTx
PA0.GPIO_Label=LIDAR_TX
PA0.Signal=USART4_TX
PA1.GPIO_Label=LIDAR_RX
PA1.Signal=USART4_RX
PA13.Signal=SYS_SWDIO
PA14-BOOT0.Signal=SYS_SWCLK
PA8.Signal=S_TIM1_CH1
PA9.Signal=S_TIM1_CH2
PB11.GPIO_Label=LED_RED
PB11.Signal=GPIO_Output
PB12.GPIO_Label=LED_ORANGE
PB12.Signal=GPIO_Output
PB13.GPIO_Label=LED_GREEN
PB13.Signal=GPIO_Output
PB14.Signal=S_TIM15_CH1
PB15.Signal=S_TIM15_CH2
PB6.GPIO_Label=BUMPER4
PB6.Signal=GPXTI6
PB7.GPIO_Label=BUMPER3
PB7.Signal=GPXTI7
PB8.GPIO_Label=BUMPER2
PB8.Signal=GPXTI8
PB9.GPIO_Label=BUMPER1
PB9.Signal=GPXTI9
PC6.Signal=S_TIM3_CH1
PC7.Signal=S_TIM3_CH2
PD0.Signal=S_TIM16_CH1
PD1.Signal=S_TIM17_CH1
PD2.GPIO_Label=BORDER_BACK
PD2.Signal=GPXTI2
PD3.GPIO_Label=BORDER_FRONT
PD3.Signal=GPXTI3
PD5.Signal=USART2_TX
PD6.Signal=USART2_RX

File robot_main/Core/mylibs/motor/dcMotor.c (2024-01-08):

/*
 * dcMotor.c
 *
 *  Created on: Oct 25, 2023
 *      Author: jkx
 */

#include "dcMotor.h"
#include "setSpeed.h"
#include "tim.h"
#include "FreeRTOS.h"
#include "task.h"
EncoderTypeDef gencodeSpeed;
EncoderTypeDef gencodeSpeed2;
MotorTypeDef gMotorData;
MotorTypeDef gMotorData2;
uint16_t Encoder_Overflow_Count = 0;
uint16_t Encoder_Overflow_Count2 = 0;

/**
 * @brief stop the motor by stop the PWM with the command: stop
 *
 */
void stopMotor(void)
{
    HAL_TIM_PWM_Stop(&htim15, TIM_CHANNEL_1);
    // HAL_TIMEx_PWMN_Stop(&htim1, TIM_CHANNEL_1);
    HAL_TIM_PWM_Stop(&htim15, TIM_CHANNEL_2);
    // HAL_TIMEx_PWMN_Stop(&htim1, TIM_CHANNEL_2);
    HAL_TIM_PWM_Stop(&htim16, TIM_CHANNEL_1);
    HAL_TIM_PWM_Stop(&htim17, TIM_CHANNEL_1);
    gMotorData.state = MOTOR_STATE_STOP;
}

/**
 * @brief start the motor by start the PWM with the command: start
 *
 */
void startMotor(void)
{
    HAL_TIM_PWM_Start(&htim15, TIM_CHANNEL_1);
    HAL_TIM_PWM_Start(&htim15, TIM_CHANNEL_2);
    HAL_TIM_PWM_Start(&htim16, TIM_CHANNEL_1);
    HAL_TIM_PWM_Start(&htim17, TIM_CHANNEL_1);
}
/**
 * @brief Set the Speed with the command : speed <speed>
 *
 * @param numberofCmdArg the number of command argument
 * @param cmdArg the command argument
 */
void setSpeed(int numberofCmdArg, char *cmdArg[])
{
    speedProcess(numberofCmdArg, cmdArg);
    gMotorData.state = MOTOR_STATE_START;
}

// founction to init the motor
void dcMotorInit(void)
{
    gencodeSpeed.encode_now = 0;
    gencodeSpeed.encode_old = 0;
    gencodeSpeed.speed = 0;
    gMotorData.state = MOTOR_STATE_STOP;
    gMotorData.direction = 1;
    gMotorData.current = 0;
    gMotorData.voltage = 0;
    gMotorData.speed = 0;
    gMotorData.motorPWM = 0;
    gencodeSpeed2.encode_now = 0;
    gencodeSpeed2.encode_old = 0;
    gencodeSpeed2.speed = 0;
    gMotorData2.state = MOTOR_STATE_STOP;
    gMotorData2.direction = 1;
    gMotorData2.current = 0;
    gMotorData2.voltage = 0;
    gMotorData2.speed = 0;
    gMotorData2.motorPWM = 0;
}
int32_t speedComputeCount = 0;
int32_t speedComputeCount2 = 0;
float speedArray[10] = {0.0};
float speedArray2[10] = {0.0};

int32_t speedArrayFilterIndex = 0;
int32_t speedArrayFilterIndex2 = 0;
void speedCompute(int encode_now, uint8_t computePerms)
{
    if (speedComputeCount == computePerms)
    {
        gencodeSpeed.encode_now = encode_now;
        gencodeSpeed.speed = (encode_now - gencodeSpeed.encode_old);
        // calculte speed motor (tour/minute) : g_encode.speed * ((1000 / 100ms) *60 )/44/20  maxspeed （300*2pi/60）  现在是rpm 每分钟
        speedArray[speedArrayFilterIndex++] = (float)(gencodeSpeed.speed * (SPEED_COMPUTE_PER_S / computePerms) * 60 / ENCODER_MODE_DIVISION / ENCODER_COUNT_PER_ROUND / GEAR_RATIO); //*RPM2RADGEAR_RATIO
        gencodeSpeed.encode_old = gencodeSpeed.encode_now;
        //  after 10 times of speed calculation, filter the speed data
        if (speedArrayFilterIndex == 10)
        {
            // bubble sort
            float temp = 0;
            for (int i = 0; i < 10; i++)
            {
                for (int j = 0; j < 10 - i - 1; j++)
                {
                    if (speedArray[j] > speedArray[j + 1])
                    {
                        temp = speedArray[j];
                        speedArray[j] = speedArray[j + 1];
                        speedArray[j + 1] = temp;
                    }
                }
            }

            temp = 0.0;
            // using the middle 6 data to calculate the average value
            for (int i = 2; i < 8; i++)
            {
                temp += speedArray[i];
            }
            // calculate the average value
            temp = temp / 6;
            // low pass filter
            // Y(n)= qX(n) + (1-q)Y(n-1)
            // X(n) is the current input, Y(n) is the current output, Y(n-1) is the previous output, and q is the filter factor.
            // The larger the q, the stronger the filtering effect, but the slower the response.
            gMotorData.speed = (float)((double)temp * 0.5 + (double)gMotorData.speed * 0.5);

            speedArrayFilterIndex = 0;
        }
        speedComputeCount = 0;
    }
    speedComputeCount++;
}

void speedCompute2(int encode_now, uint8_t computePerms)
{
    if (speedComputeCount2 == computePerms)
    {
        gencodeSpeed2.encode_now = encode_now;
        gencodeSpeed2.speed = (encode_now - gencodeSpeed2.encode_old);
        speedArray2[speedArrayFilterIndex2++] = (float)(gencodeSpeed2.speed * (SPEED_COMPUTE_PER_S / computePerms) * 60 / ENCODER_MODE_DIVISION / ENCODER_COUNT_PER_ROUND / GEAR_RATIO); //*RPM2RADGEAR_RATIO
        gencodeSpeed2.encode_old = gencodeSpeed2.encode_now;
        //  after 10 times of speed calculation, filter the speed data
        if (speedArrayFilterIndex2 == 10)
        {
            // bubble sort
            float temp = 0;
            for (int i = 0; i < 10; i++)
            {
                for (int j = 0; j < 10 - i - 1; j++)
                {
                    if (speedArray2[j] > speedArray2[j + 1])
                    {
                        temp = speedArray2[j];
                        speedArray2[j] = speedArray2[j + 1];
                        speedArray2[j + 1] = temp;
                    }
                }
            }

            temp = 0.0;
            // using the middle 6 data to calculate the average value
            for (int i = 2; i < 8; i++)
            {
                temp += speedArray2[i];
            }
            // calculate the average value
            temp = temp / 6;
            // low pass filter
            // Y(n)= qX(n) + (1-q)Y(n-1)
            // X(n) is the current input, Y(n) is the current output, Y(n-1) is the previous output, and q is the filter factor.
            // The larger the q, the stronger the filtering effect, but the slower the response.
            gMotorData2.speed = (float)((double)temp * 0.5 + (double)gMotorData2.speed * 0.5);

            speedArrayFilterIndex2 = 0;
        }
        speedComputeCount2 = 0;
    }
    speedComputeCount2++;
}

void moteur_controle(float m_gauche, float m_droite)
{
    gSpeedPID.SetPoint = m_gauche;
    gSpeedPID2.SetPoint = m_droite;
    gMotorData.state = MOTOR_STATE_START;
}

void moteur_controle_dPWM(float m_gauche, float m_droite)
{
    float gauchePWM, droitePWM;
    gauchePWM = 2560 / 300 * m_gauche;
    droitePWM = 2560 / 300 * m_droite;
    motor_pwm_set(gauchePWM);
    motor_pwm_set2(droitePWM);
}
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

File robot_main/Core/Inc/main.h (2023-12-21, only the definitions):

#define LIDAR_TX_Pin GPIO_PIN_0
#define LIDAR_TX_GPIO_Port GPIOA
#define LIDAR_RX_Pin GPIO_PIN_1
#define LIDAR_RX_GPIO_Port GPIOA
#define LED_RED_Pin GPIO_PIN_11
#define LED_RED_GPIO_Port GPIOB
#define LED_ORANGE_Pin GPIO_PIN_12
#define LED_ORANGE_GPIO_Port GPIOB
#define LED_GREEN_Pin GPIO_PIN_13
#define LED_GREEN_GPIO_Port GPIOB
#define BORDER_BACK_Pin GPIO_PIN_2
#define BORDER_BACK_GPIO_Port GPIOD
#define BORDER_BACK_EXTI_IRQn EXTI2_3_IRQn
#define BORDER_FRONT_Pin GPIO_PIN_3
#define BORDER_FRONT_GPIO_Port GPIOD
#define BORDER_FRONT_EXTI_IRQn EXTI2_3_IRQn
#define BUMPER4_Pin GPIO_PIN_6
#define BUMPER4_GPIO_Port GPIOB
#define BUMPER4_EXTI_IRQn EXTI4_15_IRQn
#define BUMPER3_Pin GPIO_PIN_7
#define BUMPER3_GPIO_Port GPIOB
#define BUMPER3_EXTI_IRQn EXTI4_15_IRQn
#define BUMPER2_Pin GPIO_PIN_8
#define BUMPER2_GPIO_Port GPIOB
#define BUMPER2_EXTI_IRQn EXTI4_15_IRQn
#define BUMPER1_Pin GPIO_PIN_9
#define BUMPER1_GPIO_Port GPIOB
#define BUMPER1_EXTI_IRQn EXTI4_15_IRQn

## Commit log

2023-10-12 nouvelle version
    [Alimentation.kicad_pcb, Alimentation.kicad_sch, Alimentation_sf.kicad_sch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]
2023-10-29 can read data from lidar ,but need to update
2023-11-29 config uart boterate 128000
2023-12-19 add ydlidar driver
2023-12-19 updata uart DMA
2023-12-19 update uart dma
2023-12-19 Update stm32g0xx_it.c by Bastien
2023-12-20 update the motorinterface
2023-12-20 add motor
2023-12-20 motor founction well
2023-12-21 motor foucntion well
2023-12-21 New stm32g0xx_it.c : Bumper interrupt by Bastien
2023-12-21 uodate the interrupt

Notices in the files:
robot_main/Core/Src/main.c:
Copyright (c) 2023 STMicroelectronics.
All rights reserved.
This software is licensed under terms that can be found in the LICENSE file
